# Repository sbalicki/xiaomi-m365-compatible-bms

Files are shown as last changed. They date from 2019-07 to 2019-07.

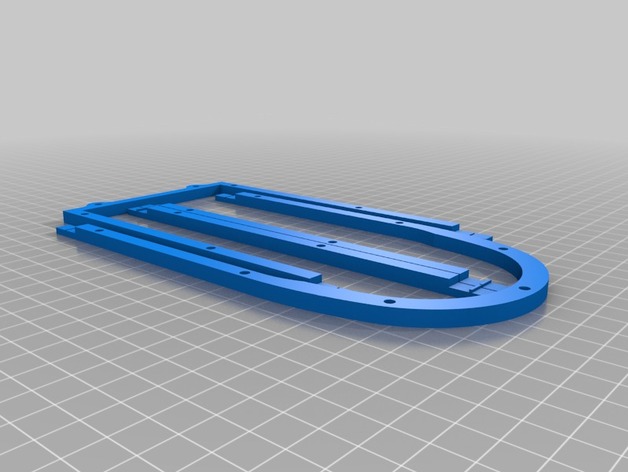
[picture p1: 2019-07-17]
hardware/3d/spacer/images/5a05439cfb2df4f365b7ed2a674fd771_preview_featured.jpg

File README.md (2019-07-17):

# Xiaomi M365 compatible BMS

#### Warning: This project is meant for people with electronics and microcontroller knowledge!

This repository contains alternative firmware for the following BMS hardware: [SP15SV0001-LLT](https://www.lithiumbatterypcb.com/product/13s-48v-li-ion-battery-pcb-board-54-6v-lithium-bms-with-60a-discharge-current-for-electric-motorcycle-and-e-scooter-protect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).  
It's programmed with the [Arduino](https://www.arduino.cc/) platform and is built with [PlatformIO](https://platformio.org/).  
It runs on an ATMega328p MCU and controls a TI BQ769x0 battery monitoring IC over I²C.

This is a fully fledged replacement BMS for the Xiaomi M365 that implements their proprietary BMS protocol and supports all of the features you'd expect, like:

 * Battery SOC (State Of Charge: mAh, %) using Coulomb Counting
 * Pack Voltage, Cell Voltages, Current, Temperature
 * Discharge and Charge cycles

All the battery information can be viewed in the native apps or 3rd party apps like [m365 Tools](https://play.google.com/store/apps/details?id=app.peretti.m365tools).

Here's some pr0n of my 12S4P NCR18650B battery: [Gallery](https://cloud.botox.bz/apps/gallery/s/94drnBJfjacBDnr).  
Materials I used:
- [Malectrics DIY Arduino Battery Spot Welder](https://malectrics.eu/product/diy-arduino-battery-spot-welder-prebuilt-kit-v3/)
- [8mm*0.2mm pure nickel strip](https://www.aliexpress.com/item/Pure-Nickel-Strip-for-Scientific-research-18650-battery-welding-Size-0-2-8mm/32739610924.html) (0.15mm is easier to weld)
- [18650 positive insulation pad](https://www.aliexpress.com/item/100Pcs-18650-lithium-battery-positive-electrode-hollow-flat-head-insulation-pad-meson-18500-positive-surface-pad/32850696072.html) **important**
- [125mm/80mm Battery PVC shrink wrap](https://www.aliexpress.com/item/125mm-Diameter-80mm-PVC-Heat-Shrink-Tubing-for-Battery-Wrap-Free-Shipping/32790874560.html)
- [50mm kapton tape](https://www.aliexpress.com/item/5-6-8-10-12-15-20-25-30-40-50MM-x-30M-Tape-Sticky-High/32889388030.html)
- I used automotive windshield glue that I had lying around, anything that sticks well to PVC should work.
- 18650 Cells: 
  - I used NCR18650B because I got them cheap.
  - Good price/performance: [Samsung INR18650-29E](https://eu.nkon.nl/samsung-inr18650-29e.html)
- Charger: Mean Well HLG-240H-48A or ELG-240-48A
  - I paid 45€ for it at [getgoods.com](https://www.getgoods.com/products/442045/Mean-Well-HLG-240H-48A-LED-driver-LED-transformer-Constant-voltage-Constant-current-240-W-5-A-48-Vdc-PFC-circuit-Surge.html) but pricing seems to vary a lot by country.
  - Look for another CC/CV power supply if this one is too expensive.

## The caveat
The BMS uses an ATMega328p MCU without an external crystal and thus has to use the internal 8 MHz resonator.  
However at 8 MHz the hardware UART will not function at 115200 baud, which is the baudrate the M365 controller expects.  
The frequency of the internal resonator can be calibrated (manually with an oscilloscope or logic analyzer) using OSCCAL to still make this work.  

But instead we simply patch the M365 firmware to use 76800 baud which works just fine with the internal 8 MHz resonator and no calibration trouble.  
Patch your firmware at [m365beta.botox.bz](https://m365beta.botox.bz/) and use the "Change ESC<->BMS baud rate to 76800" option.  
Thanks to Oleg for the idea and help.

## Hardware
### Requirements
* The BMS itself: [SP15SV0001-LLT](https://www.lithiumbatterypcb.com/product/13s-48v-li-ion-battery-pcb-board-54-6v-lithium-bms-with-60a-discharge-current-for-electric-motorcycle-and-e-scooter-protect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) or on [Aliexpress](https://www.aliexpress.com/item/12S-44-4V-smart-Lithium-li-ion-battery-protection-board-BMS-system-60A-20A-Bluetooth-phone/32976215661.html)
  * 10S - 12S. 30A version is recommended, >30A versions have both sides of the BMS PCB populated with MOSFETs and will not fit in the limited space of the M365.
* An ISP programmer with a 6pin ISP cable/adapter, example: [Aliexpress](https://www.aliexpress.com/item/10-Pin-Convert-to-Standard-6-Pin-Adapter-Board-USBASP-USBISP-AVR-Programmer-USB/2055099231.html)
* Serial UART adapter, sold by the BMS shop or on [Aliexpress](https://www.aliexpress.com/item/1PCS-CP2102-USB-2-0-to-TTL-UART-Module-6Pin-Serial-Converter-STC-Replace-FT232/32717057832.html)

### Current Shunt resistors
By default the BMS comes with ten 4mOhm shunt resistors in parallel. This results in a shunt resistance of 0.4mOhm, this is too small for accurate coulomb counting. In addition the voltage coming from the shunt resistors is also cut in half.

A simple fix for this is to simply remove some of the 4mOhm resistors so that only four resistors are left. Thus the shunt resistance will be 1mOhm.  
And to fix the shunt voltage from getting cut in half two more small resistors are removed from the top layer, as in the pictures: [Bottom](https://cloud.botox.bz/s/J6oZWqJDikzpTw8/preview) and [Top](https://cloud.botox.bz/s/2ipzTsJNWQ222TH/preview).

### Wiring
#### IMPORTANT: The M365 ESC - connects to P- of the BMS!
**Otherwise the M365 will be damaged when you brake with a full battery due to overvoltage!**

**C- has to be used to charge the battery, otherwise the BMS offers no protection against faulty chargers/overvoltage!**

**Do not cut the big - trace on the M365 ESC or it will damage the BMS because of different GND potentials on UART!**

**Do not connect GND from the BMS to the M365 anywhere! P- is GND for the M365! The only extra wires going from the BMS to the M365 are RX and TX!**

### Battery cover spacer
New battery is thicker than the original one so you will need an additional spacer between the battery cover and the M365 board. The sample 3D model is in hardware/3d/spacer.

Source: [M365 battery spacer](https://www.thingiverse.com/thing:3731368).

## Software
### Configuration
Depending on your battery you might want to configure some of the settings here: [src/main.h](src/main.h#L24)

* `capacity`: The *actual* total capacity in mAh of your battery pack, don't use the manufacturer stated capacity if you want to have accurate SOC but rather look at sites like [lygte-info.dk](https://lygte-info.dk/), etc.
  * Example: for 4 * NCR18650B I used a value of 12400mAh.
* `nominal_voltage`: The nominal voltage in mV of your cells, this will be 3.6V for almost all cells.
* `full_voltage`: The voltage in mV that you will charge your cells to. I only charge mine to 4.1V for cycle life.
* `ODP_current`: Over current protection value in mA, if your scooter is shutting off on your crazy settings then make this higher.
* `UVP_voltage`: The BMS will shut off P- when any cells voltage goes below this.
  * Remember: During load the cell voltage will drop a lot.
* `OVP_voltage`: The BMS will shut off C- when any cells voltage goes above this.
  * So do not connect your M365 ESC to C- or it'll die when you brake with a full battery, use P- for the ESC and C- to charge!

If you've already flashed and run the firmware on your BMS you can only make changes using `configtool.py` (since the settings are written to EEPROM).  
Use `getSettings()` to populate g_Settings, then make changes like so: `g_Settings.capacity = 7800`.  
If you're done with making changes use: `putSettings()` to push them to the BMS, use `applySettings()` to apply them and `saveSettings()` to write them to EEPROM.

### Compiling
This project uses [PlatformIO](https://platformio.org/), please check out their [Documentation](https://docs.platformio.org/en/latest/) to get started.

### Programming bootloader via ISP
Connect your ISP programmer to the BMS, you can (and should) keep the battery disconnected while programming.  
Here's the pinout of the ISP header: [Image](https://cloud.botox.bz/s/qGa7rS6Ktt4pG24/preview)  
On the new V1.5 PCB it's a little trickier: [Image1](https://cloud.botox.bz/s/eYmBCM4Z44P84tj/preview) [Image2](https://cloud.botox.bz/s/7BkSS7NKk878B4d/preview)

Flash the bootloader with [AVRDUDE](https://download.savannah.gnu.org/releases/avrdude/avrdude-6.3-mingw32.zip) using the following command: `avrdude -patmega328p -cstk500v2 -P/dev/ttyUSB0 -U lfuse:w:0xE2:m -U hfuse:w:0xDE:m -U efuse:w:0xFD:m -U lock:w:0xFF:m -U flash:w:optiboot_atmega328.hex`  
Adjust the `-P/dev/ttyUSB0` part to the correct COM port on your PC.

### Uploading/Updating firmware
You can upload the firmware in platformio, there's a little arrow somewhere.  
You have to short the RESET pin to GROUND right before you hit the upload button!  
For updating firmware you don't have to short the RESET pin but can run `bootloader.py /dev/ttyUSB0` right before you hit upload.

## Troubleshooting
Have you patched your M365 firmware for 76800 baud?

Make sure the temperature sensors are plugged in and all wires are connected properly.
B- needs to be connected to the battery -.

Reset the BMS by shorting GND with RST on the ISP header.

Run `configtool.py /dev/ttyUSB0` in an interactive python shell (IDLE on Windows, `python -i` on Linux) with the correct COM port.  
You'll probably have to install these two dependencies: [cstruct](https://pypi.org/project/cstruct/) and [pyserial](https://pypi.org/project/pyserial/).  
Check the source code for commands you can use, though you'll probably only need `debug_print()`.
You can also use any serial terminal and send this string in HEX `55aa0322fa0500dbfe` instead of `debug_print()`.  
Since the controller will enter sleep mode after 5 seconds of inactivity you'll have to send this twice quickly when using a serial terminal.

## M365
After you've checked that your BMS works (voltage between + and P-) and communicates via UART (it print's `BOOTED!` when it boots) you can connect it with your M365.

The original BMS was connected to the top 3pin header on the M365 ESC: [Image](https://cloud.botox.bz/s/QLzWYc9C253QECi/preview)  
You'll have to connect the ESC **R** pin to the BMS **TX** pin and the **T** pin to the **RX** pin.  
The ESC **L** pin is + for the red/brake light on the back fender, you'll have to make your own cable for that.

## Final words
### Credits
A big part of the BQ769x0 code is taken from here: [LibreSolar/bq769x0_mbed_lib](https://github.com/LibreSolar/bq769x0_mbed_lib).

### Support
If you've spent at least an hour with your issue you can ask about it nicely in my [M365 Telegram group](https://t.me/XiaomiM365Hacking).

### Disclaimer
If you break anything it's your own fault.  
**Works for me™.** is the only guarantee I can give you.

I am in no way affiliated with the company that makes the BMS. I just bought it, reversed some stuff and made this firmware.

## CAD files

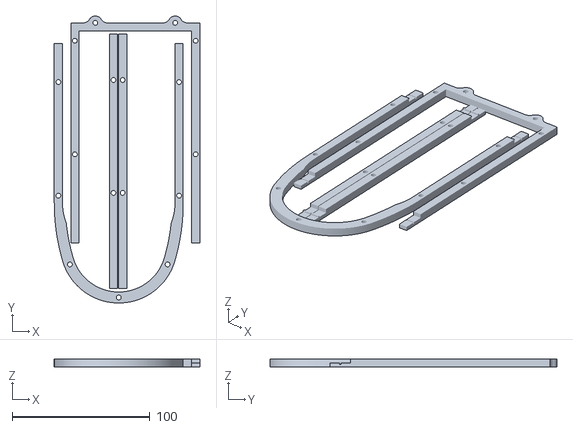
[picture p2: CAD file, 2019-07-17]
hardware/3d/spacer/files/m365_bottom_ext2_5.5mm.stl
105.7 x 208.5 x 5.50

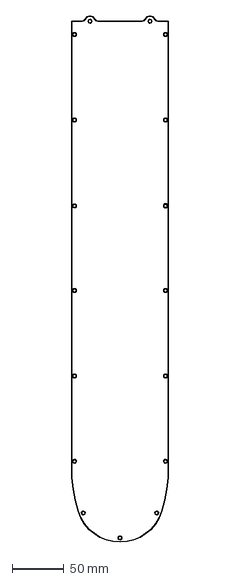
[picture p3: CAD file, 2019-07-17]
hardware/3d/spacer/files/m365_bottom.dxf
93.7 x 508.5 mm

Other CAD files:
hardware/3d/spacer/files/m365_bottom_ext2_5.5mm.f3d
